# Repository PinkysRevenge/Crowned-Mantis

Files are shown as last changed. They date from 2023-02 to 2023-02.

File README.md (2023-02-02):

# Crowned-Mantis
## A CPAP toolhead for Voron Trident and v2.4

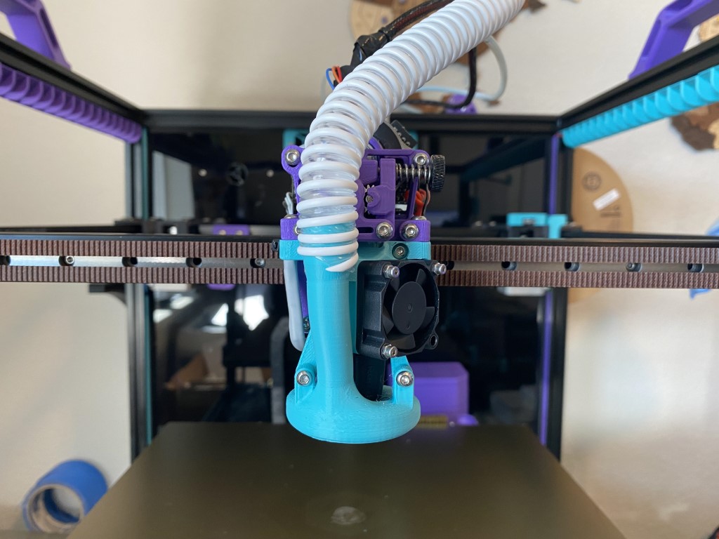
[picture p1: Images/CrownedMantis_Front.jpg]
Crowned-Mantis


This project is still in early development. Use at your own risk and please provide feedback. 

Discord: Pinky’s Revenge#0561

Credits - this toolhead uses:
 - A modified duct from the CrownCooler toolhead by SneakyTreeSnake (https://github.com/sneakytreesnake/CrownCooler)
 - The X Carriage and magprobe of the Mantis Toolhead by Long (https://github.com/VoronDesign/VoronUsers/tree/master/printer_mods/Long/Mantis_Dual_5015)
 - CPAP sourcing and setup instructions by Chirpy (https://github.com/chirpy2605/voron/tree/main/V0/StovePipe)

## BOM

- Rapido HF Hotend (if you'd like a version for another hotend, let me know)
- Sherpa Mini Extruder (I plan to make a version for Orbiter/VZ-Hextrudor soon) 
- 3010 hot end fan
- CPAP fan, controller, and 15mm ID CPAP hose (see below for more details on CPAP setup)
- Mantis carriage and magprobe setup
- 5x 3mm heat set inserts (not including others needed for the Mantis carriage and Sherpa Mini
- 3x 2mm heat set inserts (if you want a version that uses 3mm let me know)
- Various 3mm and 2mm screws

## Parts to Print
1. Mantis carriage and magprobe parts according to the github here: https://github.com/VoronDesign/VoronUsers/tree/master/printer_mods/Long/Mantis_Dual_5015
2. Sherpa Mini extruder parts according to the gitbhub here: https://github.com/Annex-Engineering/Sherpa_Mini-Extruder
3. Crowned-Mantis_HE_Mount. Does require supports (touching build plate only), otherwise use standard Voron print specs.
4. Crowned-Mantis_Duct. Recommend 0.1mm layer height. Supports (touching build plate only) can be helpful for the outlets if your bridging isn't great, but they aren't necessary.
5. Optional: Crowned-Mantis_Sherpa_Housing_Front replaces the normal Sherpa Mini Housing_Front for added stiffness
6. Optional: Simon Vez has a great CPAP fan mount and outlet adapter here: https://github.com/VzBoT3D/Vz-Printhead-CNC/tree/main/CAD/CPAP%20turbo%20cooling%20systemhttps://github.com/VzBoT3D/Vz-Printhead-CNC/tree/main/CAD/CPAP%20turbo%20coo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

## Toolhead Assembly

1. Build the Mantis carriage and magprobe according to the github
2. Build the Sherpa Mini extruder according to the gitbhub
3. Install 5x 3mm heat inserts into the HE mount to hold the duct and the extruder

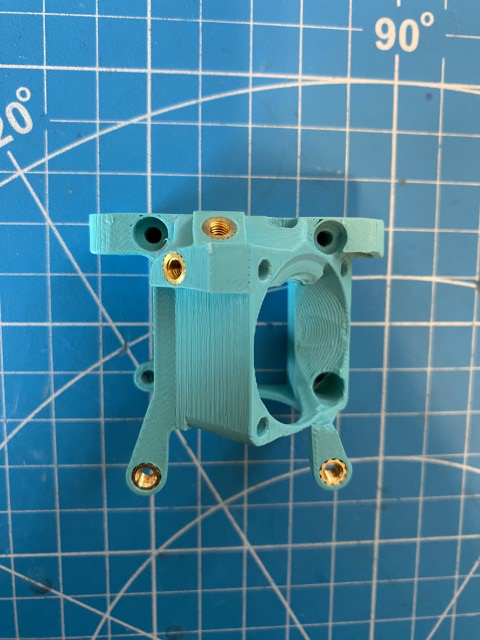
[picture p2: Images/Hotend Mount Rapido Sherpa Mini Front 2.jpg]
Front_View


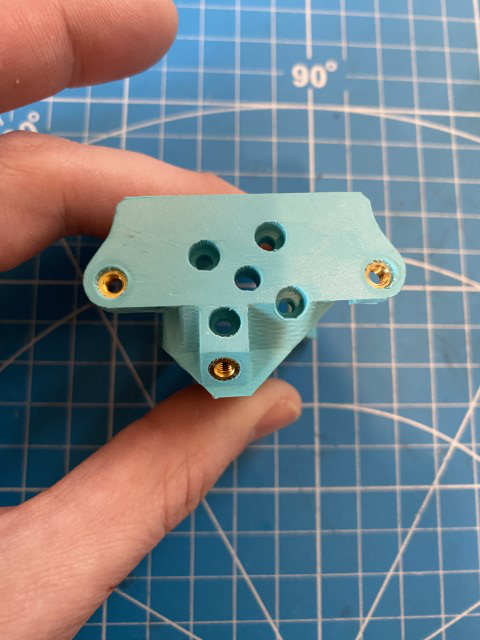
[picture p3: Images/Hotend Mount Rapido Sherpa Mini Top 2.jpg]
Top_View


4. Install 3x 2mm heat inserts into the HE mount to hold the fan

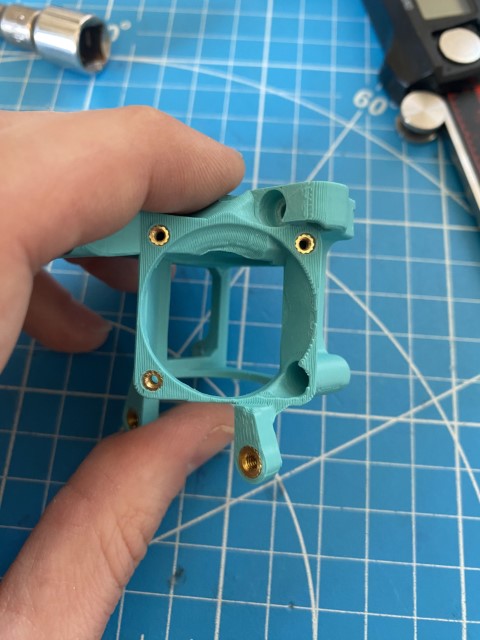
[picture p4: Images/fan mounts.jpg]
Fan_Mounts


6. Screw the hot end to the HE mount
7. Screw the HE mount to the Mantis carriage
8. Screw the Sherpa Mini, HE fan and duct to the HE mount

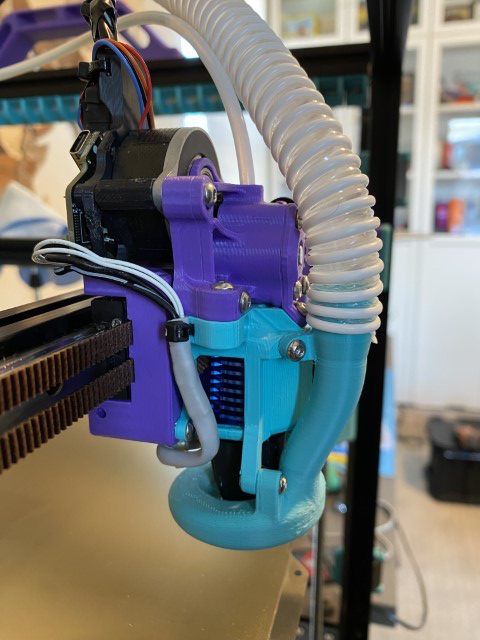
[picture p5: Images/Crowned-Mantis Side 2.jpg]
Side_View


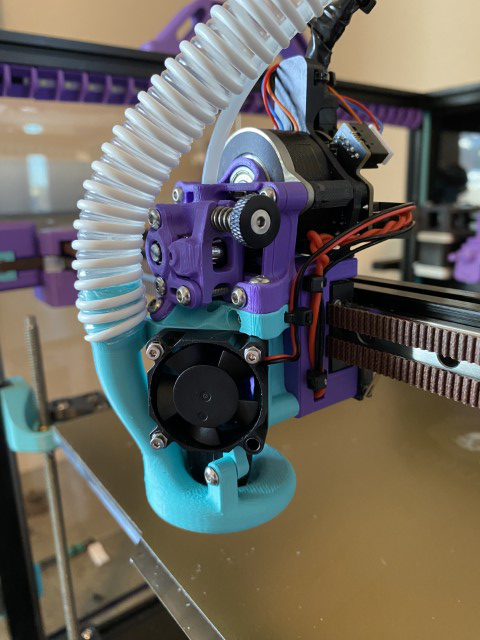
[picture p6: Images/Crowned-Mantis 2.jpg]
Crowned-Mantis


## CPAP Sourcing and Setup

CPAP fans not only have a high CFM, they generally also have very high static pressure. This allows air to be delivered to the hotend with greater force than traditional blower fans.

This mod uses the WS7040-24-V200 from Wonsmart which needs to be sourced with a supported driver board. This allows the fan to run at 24v, but the fans PWM is controlled by a 5v data logic controller.

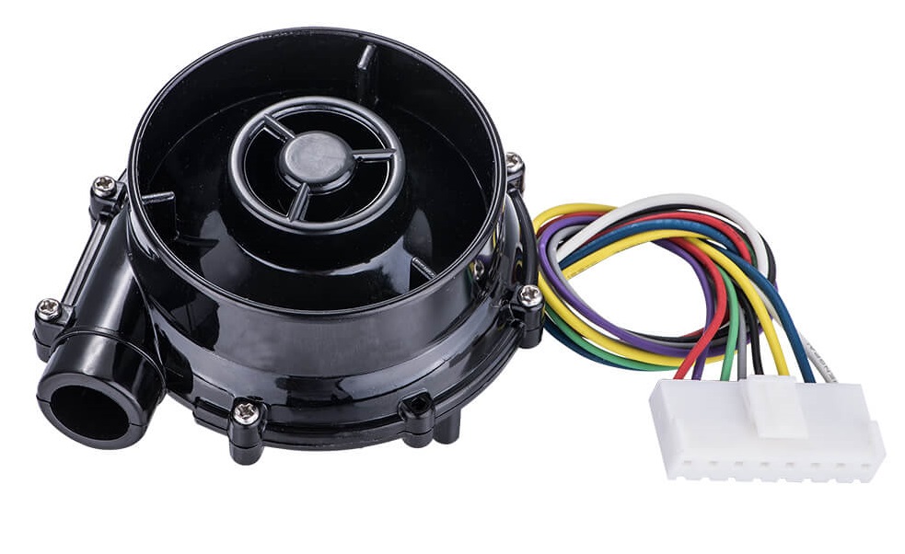
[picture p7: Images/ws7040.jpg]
ws7040

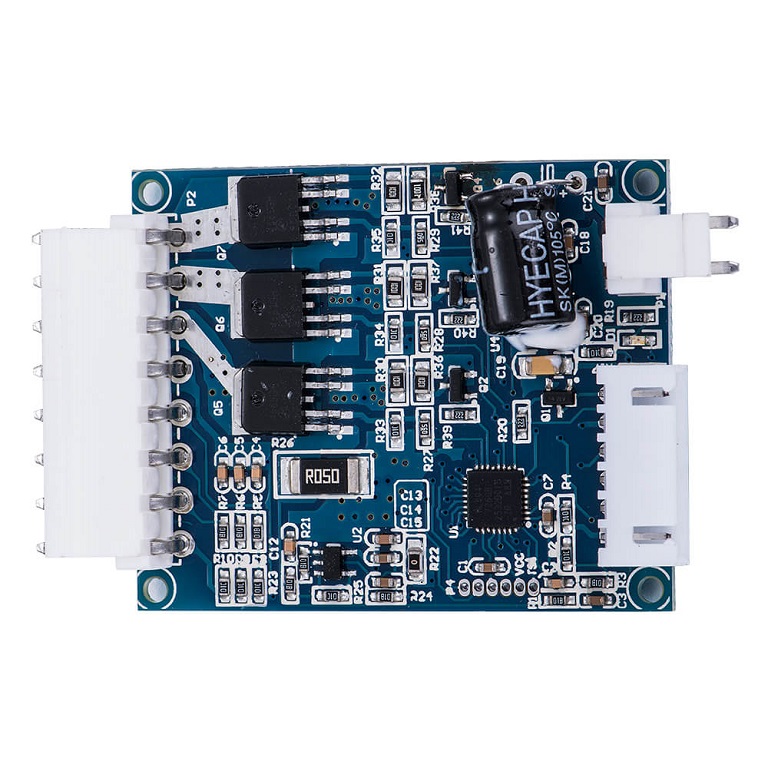
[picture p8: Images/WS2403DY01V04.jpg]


It can also be controlled by a 3.3V  data logic controller such as the printers MCU, but you will usually be limited to ~60% of the fans potential. To increase this you can use a logic level converter to translate the 3.3v data signal to 5v.

This can be achieved in various ways, e.g. using an MCU's neopixel port since they must be driven by 5v data logic. Alternatively, a dedicated logic level converter can be connected to a spare port on the raspberry PI, such as the [Sparkfun BOB-12009](https://www.sparkfun.com/products/12009) which works very well.

The main disadvantage of only using a logic level shifter is that the fan will run at 100% when power is first fed to the PI pin as it floats before being explicitly set. This can be countered by powering the fan itself through a spare heater port on the MCU which you may have free and using it as an enable pin in klipper.

As a simple solution that addresses all of these requirements and concerns, I'm using the [Klipper Expander](https://github.com/VoronDesign/Voron-Hardware/tree/master/Klipper_Expander). The advantages with this solution is that you can control the fan through the Neopixel pin (only 1 wire needed) and explicitly power the fan on/off through one of the 24v MOSFETs. This is important because traditional 24v MCU fan headers won't usually support the 2.8A that this fan can pull at 100% load which can lead to a damaged MCU. 

This mod works optimally with a 15mm ID CPAP hose such as [this one](https://www.amazon.co.uk/gp/product/B07TCC42WT) that I have used. They can also be found on Aliexpress.

The simplest way to purchase the WS7040 fan is through [Mellow on Aliexpress](https://www.aliexpress.com/item/1005004729010078.html) as this comes together with the required driver board and at the correct voltage. [Trianglelab](https://www.aliexpress.com/item/1005003822117604.html) also have a complete kit, however the included CPAP hose is not 15mm ID and won't work directly with this implementation. There are many other sellers for the WS7040 at widely varying prices. Just be sure to get the correct model (WS7040-24-V200) together with the associated [driver board](https://www.wonsmart.com.cn/ws2403-15655936300127195.html).

## Wiring:

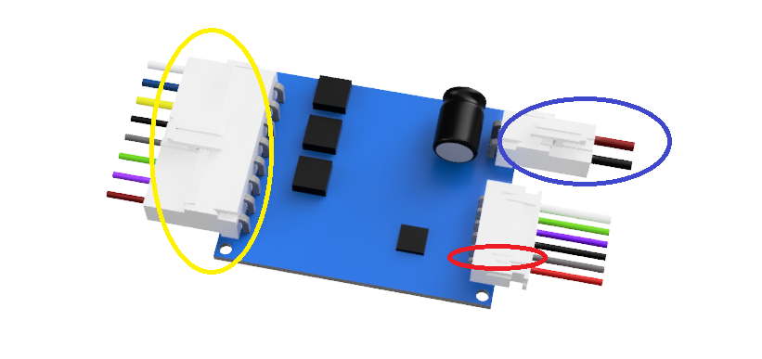
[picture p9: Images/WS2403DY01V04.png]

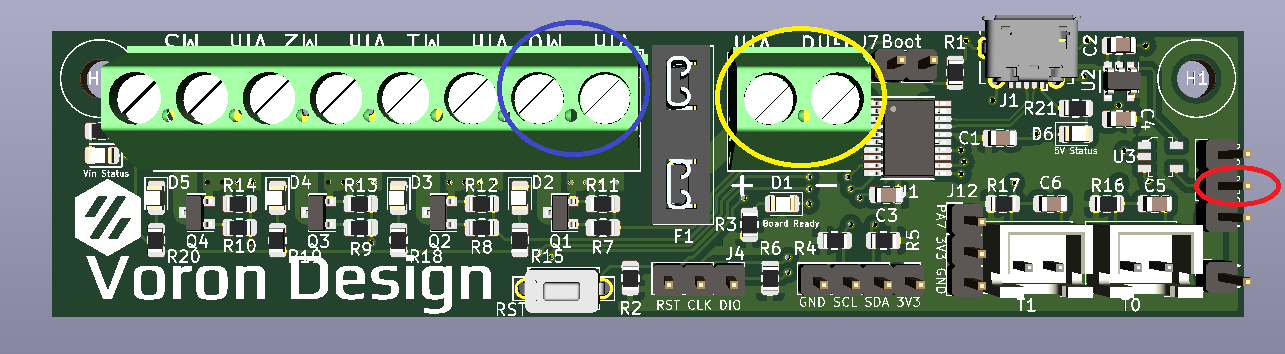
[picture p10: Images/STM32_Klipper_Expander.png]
Klipper Expander


Run a wire from the second from the bottom pin (red circle) on the driver board to the centre neopixel pin (red circle) on the klipper expander.

Connect the 24v connector (blue circle) on the driver board to one of the MOSFET ports (blue circle) on the Klipper Expander, paying attention to the polarity.

Connect the large connector from the fan to the driver board (yellow circle).

Connect your 24v supply (e.g. from the printer PSU) to the Klipper Expander (yellow circle). See the [Klipper Expander](https://github.com/VoronDesign/Voron-Hardware/tree/master/Klipper_Expander/Documentation) documentation on how to connect and configure it to the printer.

Buy me a coffee
https://www.buymeacoffee.com/PinkysRevenge

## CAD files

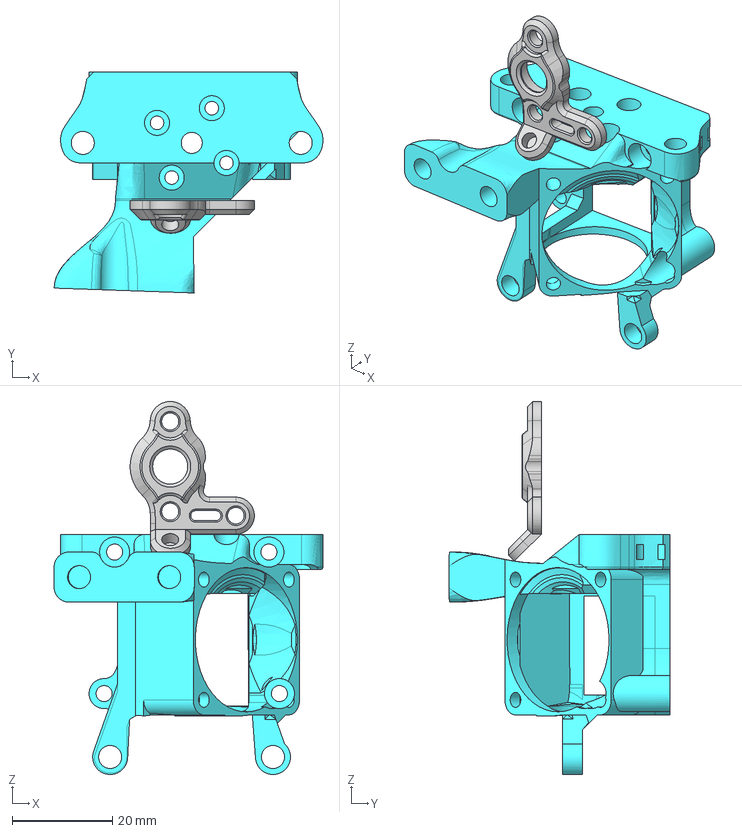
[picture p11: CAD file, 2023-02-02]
CAD/Crowned-Mantis_Sherpa_Housing_Front.step
53.7 x 44.1 x 74.5 mm
Carriage
EBB36 sherpa mini mount overmold strain relief v1
CrownedMantis_HE Mount 3mm mounts
Crown Cooler Smaller Duct v7

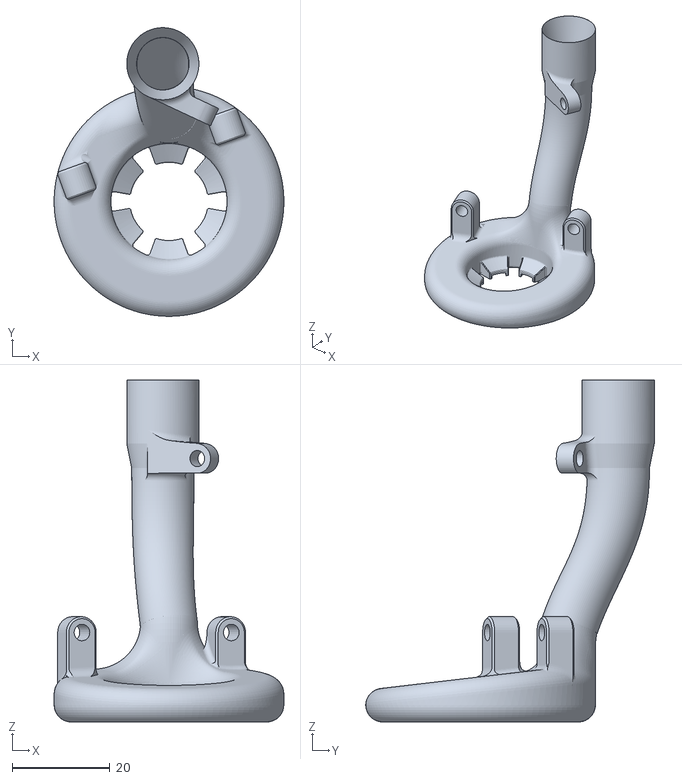
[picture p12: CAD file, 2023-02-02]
STLs/Crowned-Mantis_Duct.stl
47.0 x 59.0 x 70.0

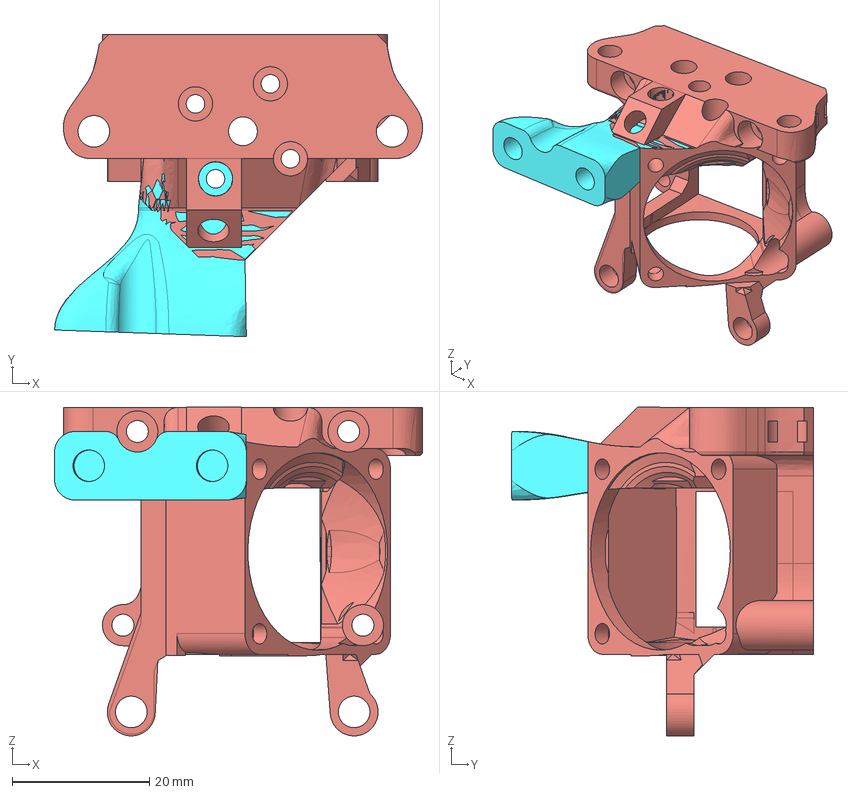
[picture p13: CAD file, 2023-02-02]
CAD/Crowned-Mantis_HE_Mount.step
53.7 x 44.1 x 48.0 mm
Carriage
EBB36 sherpa mini mount overmold strain relief v1
CrownedMantis_HE Mount 3mm mounts
Crown Cooler Smaller Duct v7

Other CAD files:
STLs/Crowned-Mantis_HE_Mount.stl
STLs/Crowned-Mantis_Sherpa_Housing_Front.stl
